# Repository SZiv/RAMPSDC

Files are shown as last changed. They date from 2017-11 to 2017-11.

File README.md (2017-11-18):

# RAMPSDC
RAMPS Due Converter. 
See the Wiki here: http://reprap.org/wiki/RAMPSDC (still working on it)

Goes between a standard 5V RAMPS, and a 3.3V Arduino Due. Uses the Vin from the RAMPS board to power the 5V rail, and then uses that 5V supply to power pins on the RAMPS, allowing more current for the Heater and Servo pins outputs. 
Steps down voltage of the X Max, Y max, Y min, Xmin, and Z min endstops (The Z MAX Enstop is unconnected), so they dont damage the Due, and a 5V-3.3V voltage divider is used to propotionally drop the voltage of the Thermistors.
Also adds the EEPROM required for use as a 3D printer controller.

Uses three generic bidirectional level shifter modules (two if you arn't using servos). These can be bought from Ebay or Aliexpress for maybe 50 cents each. Just make sure you get the kind with the powers and grounds (HV, GND, LV, GND) in the middle. Other than that, its a pretty generic part.

Most other pins are connected to the RAMPS as if it was a mega (Digital pin 51 > digital pin 51, RX > RX, TX > TX, ETC). It is worth noting that since the pins dont perfectly match up, I2C 1 (which is normally broken out on the RAMPS), is used by the EEPROM, so the 2nd I2C header is broken out on the RAMPS. The SPI pins are not in the same place as the mega, and are broken out behind the RAMPS connector.

As a reminder, all inputs, INCLUDING the Analog inputs, MUST be reduced to 3.3V before hitting the due. This means you cannot use an LCD screen with this, without some sort of voltage regulation on the encoder. I'm still working on a workaround for this, and that may show up in V2.

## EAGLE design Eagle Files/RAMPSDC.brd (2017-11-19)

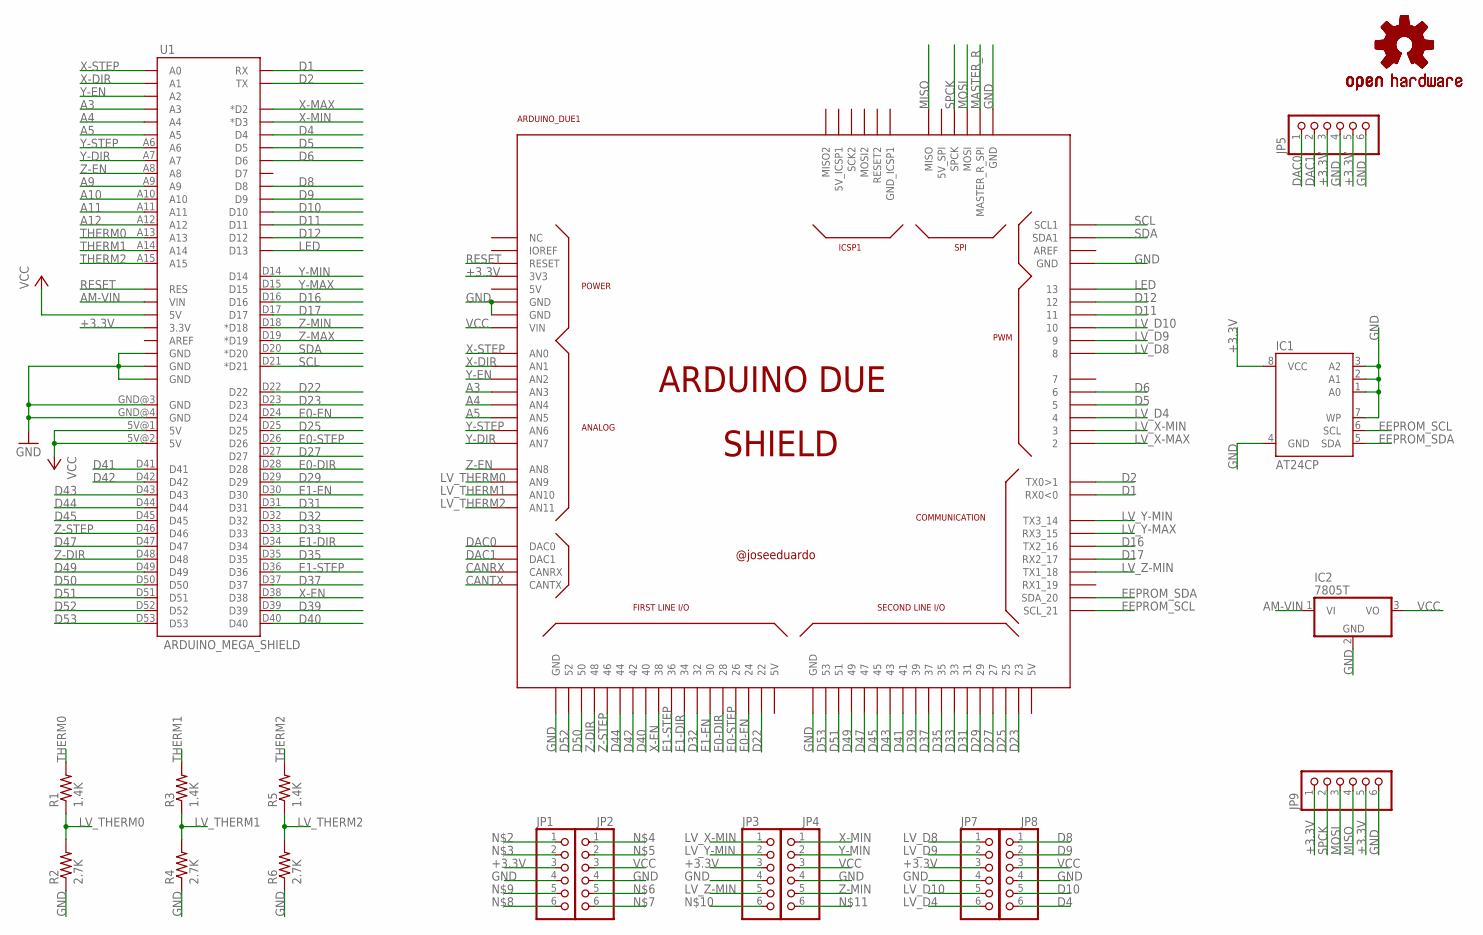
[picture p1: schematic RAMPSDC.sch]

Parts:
ARDUINO_DUE1: ARDUINO_DUE_SHIELD
IC1: AT24CP; DIL08
IC2: 7805T; TO220H
JP1, JP2, JP3, JP4, JP5, JP7, JP8, JP9: PINHD-1X6; 1X06
LOGO1: OSHW-LOGOS; OSHW-LOGO-S
LOGO2: OSHW-LOGOL-COPPER; OSHW-LOGO-L_COPPER
R1, R3, R5: 1.4K; R0805
R2, R4, R6: 2.7K; R0805
U1: ARDUINO_MEGA_SHIELD

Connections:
+3.3V: ARDUINO_DUE1.3V3, IC1.8 (VCC), JP1.3, JP3.3, JP5.3, JP5.5, JP7.3, JP9.1, JP9.5, U1.3.3V
A3: ARDUINO_DUE1.A3 (AN3), U1.A3
A4: ARDUINO_DUE1.A4 (AN4), U1.A4
A5: ARDUINO_DUE1.A5 (AN5), U1.A5
A9: U1.A9
A10: U1.A10
A11: U1.A11
A12: U1.A12
AM-VIN: IC2.1 (VI), U1.VIN
CANRX: ARDUINO_DUE1.CANRX
CANTX: ARDUINO_DUE1.CANTX
D1: ARDUINO_DUE1.0 (RX0<0), U1.RX
D2: ARDUINO_DUE1.1 (TX0>1), U1.TX
D4: JP8.6, U1.D4
D5: ARDUINO_DUE1.5, U1.D5
D6: ARDUINO_DUE1.6, U1.D6
D8: JP8.1, U1.D8
D9: JP8.2, U1.D9
D10: JP8.5, U1.D10
D11: ARDUINO_DUE1.11, U1.D11
D12: ARDUINO_DUE1.12, U1.D12
D16: ARDUINO_DUE1.16 (TX2_16), U1.D16
D17: ARDUINO_DUE1.17 (RX2_17), U1.D17
D22: ARDUINO_DUE1.22, U1.D22
D23: ARDUINO_DUE1.23, U1.D23
D25: ARDUINO_DUE1.25, U1.D25
D27: ARDUINO_DUE1.27, U1.D27
D29: ARDUINO_DUE1.29, U1.D29
D31: ARDUINO_DUE1.31, U1.D31
D32: ARDUINO_DUE1.32, U1.D32
D33: ARDUINO_DUE1.33, U1.D33
D35: ARDUINO_DUE1.35, U1.D35
D37: ARDUINO_DUE1.37, U1.D37
D39: ARDUINO_DUE1.39, U1.D39
D40: ARDUINO_DUE1.40, U1.D40
D41: ARDUINO_DUE1.41, U1.D41
D42: ARDUINO_DUE1.42, U1.D42
D43: ARDUINO_DUE1.43, U1.D43
D44: ARDUINO_DUE1.44, U1.D44
D45: ARDUINO_DUE1.45, U1.D45
D47: ARDUINO_DUE1.47, U1.D47
D49: ARDUINO_DUE1.49, U1.D49
D50: ARDUINO_DUE1.50, U1.D50
D51: ARDUINO_DUE1.51, U1.D51
D52: ARDUINO_DUE1.52, U1.D52
D53: ARDUINO_DUE1.53, U1.D53
DAC0: ARDUINO_DUE1.DAC0, JP5.1
DAC1: ARDUINO_DUE1.DAC1, JP5.2
E0-DIR: ARDUINO_DUE1.28, U1.D28
E0-EN: ARDUINO_DUE1.24, U1.D24
E0-STEP: ARDUINO_DUE1.26, U1.D26
E1-DIR: ARDUINO_DUE1.34, U1.D34
E1-EN: ARDUINO_DUE1.30, U1.D30
E1-STEP: ARDUINO_DUE1.36, U1.D36
EEPROM_SCL: ARDUINO_DUE1.21 (SCL_21), IC1.6 (SCL)
EEPROM_SDA: ARDUINO_DUE1.20 (SDA_20), IC1.5 (SDA)
GND: ARDUINO_DUE1.GND, ARDUINO_DUE1.GND_1 (GND), ARDUINO_DUE1.GND_2 (GND), ARDUINO_DUE1.GND_3 (GND), ARDUINO_DUE1.GND_4 (GND), ARDUINO_DUE1.GND_5 (GND), IC1.1 (A0), IC1.2 (A1), IC1.3 (A2), IC1.4 (GND), IC1.7 (WP), IC2.2 (GND), JP1.4, JP2.4, JP3.4, JP4.4, JP5.4, JP5.6, JP7.4, JP8.4, JP9.6, R2.1, R4.1, R6.1, U1.GND@0 (GND), U1.GND@1 (GND), U1.GND@2 (GND), U1.GND@3 (GND), U1.GND@4 (GND)
LED: ARDUINO_DUE1.13, U1.D13
LV_D4: ARDUINO_DUE1.4, JP7.6
LV_D8: ARDUINO_DUE1.8, JP7.1
LV_D9: ARDUINO_DUE1.9, JP7.2
LV_D10: ARDUINO_DUE1.10, JP7.5
LV_THERM0: ARDUINO_DUE1.A9 (AN9), R1.1, R2.2
LV_THERM1: ARDUINO_DUE1.A10 (AN10), R3.1, R4.2
LV_THERM2: ARDUINO_DUE1.A11 (AN11), R5.1, R6.2
LV_X-MAX: ARDUINO_DUE1.2
LV_X-MIN: ARDUINO_DUE1.3, JP3.1
LV_Y-MAX: ARDUINO_DUE1.15 (RX3_15)
LV_Y-MIN: ARDUINO_DUE1.14 (TX3_14), JP3.2
LV_Z-MIN: ARDUINO_DUE1.18 (TX1_18), JP3.5
MASTER_R: ARDUINO_DUE1.MASTER_RESET_SPI (MASTER_R_SPI)
MISO: ARDUINO_DUE1.MISO, JP9.4
MOSI: ARDUINO_DUE1.MOSI, JP9.3
RESET: ARDUINO_DUE1.RESET, U1.RES
SCL: ARDUINO_DUE1.SCL1, U1.D21 (*D21)
SDA: ARDUINO_DUE1.SDA1, U1.D20 (*D20)
SPCK: ARDUINO_DUE1.SPCK, JP9.2
THERM0: R1.2, U1.A13
THERM1: R3.2, U1.A14
THERM2: R5.2, U1.A15
VCC: ARDUINO_DUE1.VIN, IC2.3 (VO), JP2.3, JP4.3, JP8.3, U1.5V@0 (5V), U1.5V@1 (5V), U1.5V@2 (5V)
X-DIR: ARDUINO_DUE1.A1 (AN1), U1.A1
X-EN: ARDUINO_DUE1.38, U1.D38
X-MAX: U1.D2 (*D2)
X-MIN: JP4.1, U1.D3 (*D3)
X-STEP: ARDUINO_DUE1.A0 (AN0), U1.A0
Y-DIR: ARDUINO_DUE1.A7 (AN7), U1.A7
Y-EN: ARDUINO_DUE1.A2 (AN2), U1.A2
Y-MAX: U1.D15
Y-MIN: JP4.2, U1.D14
Y-STEP: ARDUINO_DUE1.A6 (AN6), U1.A6
Z-DIR: ARDUINO_DUE1.48, U1.D48
Z-EN: ARDUINO_DUE1.A8 (AN8), U1.A8
Z-MAX: U1.D19 (*D19)
Z-MIN: JP4.5, U1.D18 (*D18)
Z-STEP: ARDUINO_DUE1.46, U1.D46

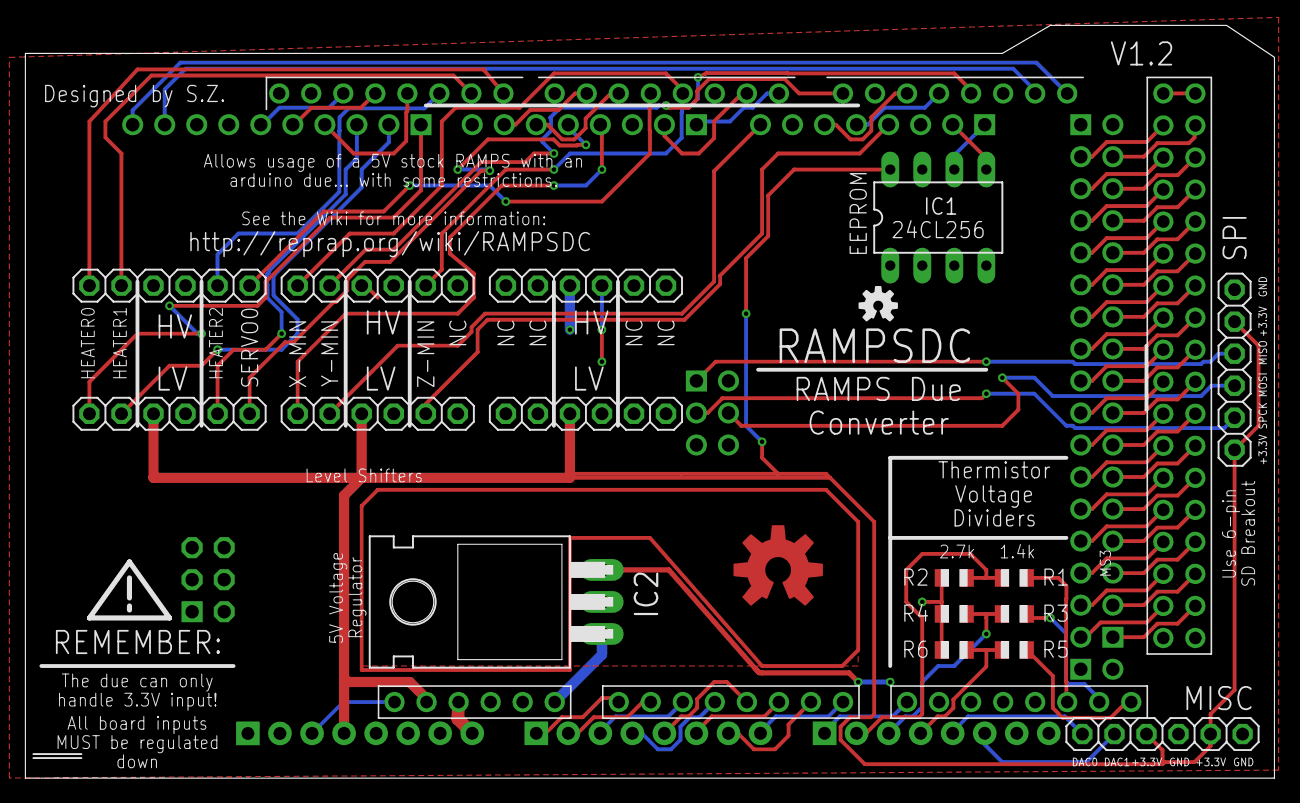
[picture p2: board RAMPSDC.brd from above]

Board: 2 copper layers, 99.1 x 59.7 mm, 20 parts (0 on the bottom side), 84 nets.

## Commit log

2017-11-18 First Commit! Kachow!
    initial commit
    [RAMPSDC.GBL, RAMPSDC.GBO, RAMPSDC.GBP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]
2017-11-19 Fixed a critical issue with the Step-downs.
    They are actually seperated by 5 pins, not 6. Derp! Fixed. I'm working
    on a new revision that will get rid of the maximum endstops and servos
    2-4 (disconnect completely), and use that spare driver to regulate an
    LCD screen down, or at least make pinouts for an SD ramps
    [RAMPSDC.brd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]
2017-11-19 Disconnected Max Endstops and Servos 2-4. Added SD card Headers. Fixed some Silkscreen errors.
    This is a step towards making the LCD screen work, but in the meantime,
    the last level shifter was changed to all NC. At some point, that will
    be the encoder button, encoder 1, encoder 2, MISO, and whatever else
    needs to be shifted to make the reprap full graphics controller work.
    The issue is the documentation sucks on that so I need to really dig to
    make it work. In the meantime, I added just a breakout header for the
    generic 6-pin SD card module for arduinos. This doesnt replace an LCD,
    but at least makes it run standalone.
    The Max Endstops were not rerouted to anywhere, and are disconnected
    fr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
    [RAMPSDC.brd, RAMPSDC.sch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]

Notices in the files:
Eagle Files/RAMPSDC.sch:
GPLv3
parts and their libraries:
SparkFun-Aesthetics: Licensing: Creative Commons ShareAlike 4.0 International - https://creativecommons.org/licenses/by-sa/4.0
